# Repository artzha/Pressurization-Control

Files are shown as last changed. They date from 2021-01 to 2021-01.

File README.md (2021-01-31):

# Pressurization-Control
Designed by Josh Azrin and Arthur Zhang.

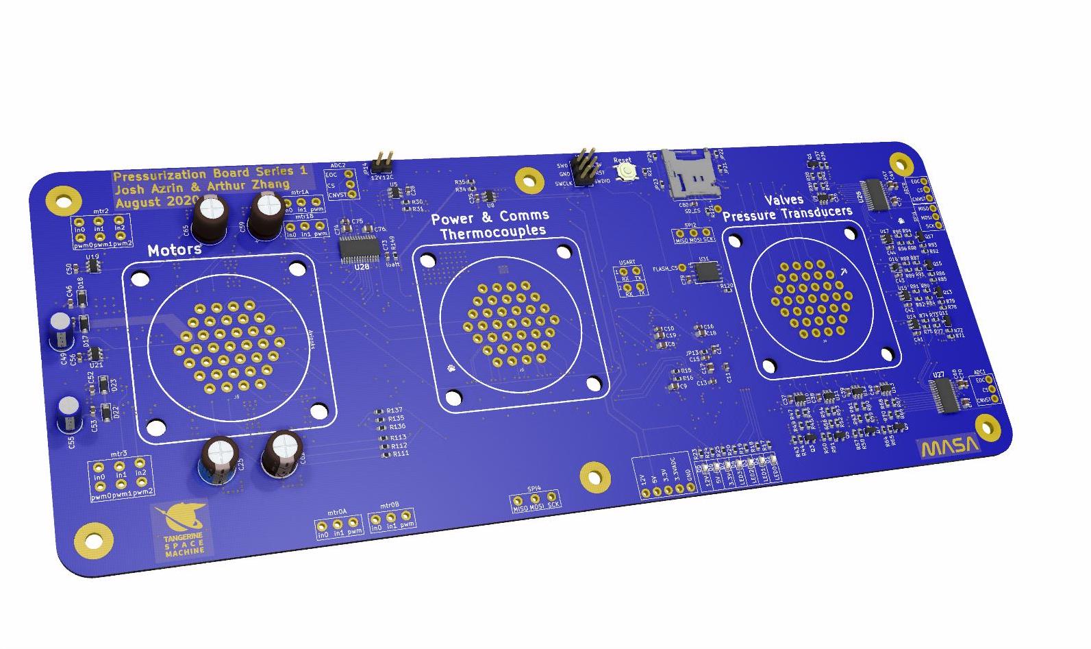
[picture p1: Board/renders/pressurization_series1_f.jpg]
Board Front

|:--:| 
| *Front of PCB* |

Combustion-Control is a project that Josh and I researched and designed to actively balance the liquid fuel tanks for rockets using a PID control loop and various peripherals. We are currently working with the ATLO team to integrate their custom PID control loop into this system. Currently, we are using this PCB on Tangerine Space Machine, a rocket that students are designing at Michigan Aeronautics and Science Association (MASA), a project design team at the University of Michigan.

## Project Overview
1. Overview
1. Board Specs
2. Key Features
3. Firmware Architecture
4. Additional Information

## Overview

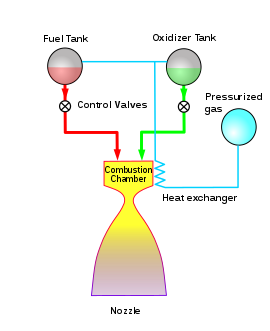
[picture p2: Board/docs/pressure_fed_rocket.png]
Pressure Explanation

|:--:| 
| *Diagram of Pressure Fed Rocket* |

Liquid fuel rockets typically use a pressurized gas like helium to force fuel and oxidizer together into a combustion chamber. In order to maintain a steady combustion, we must ensure that the tank pressures exceed the combustion chamber pressure. We plan on accomplishing this by controlling the flow rate of the the fuel and oxidizer together using a needle valve. This method uses simple plumbing and removes the need for complex turbopumps. Along with Josh, we designed a PCB that supports this functionality. In addition, I have also architected the firmware for carrying out PID control, Command and Data Handling, and interfacing with peripherals.

## Board Specs

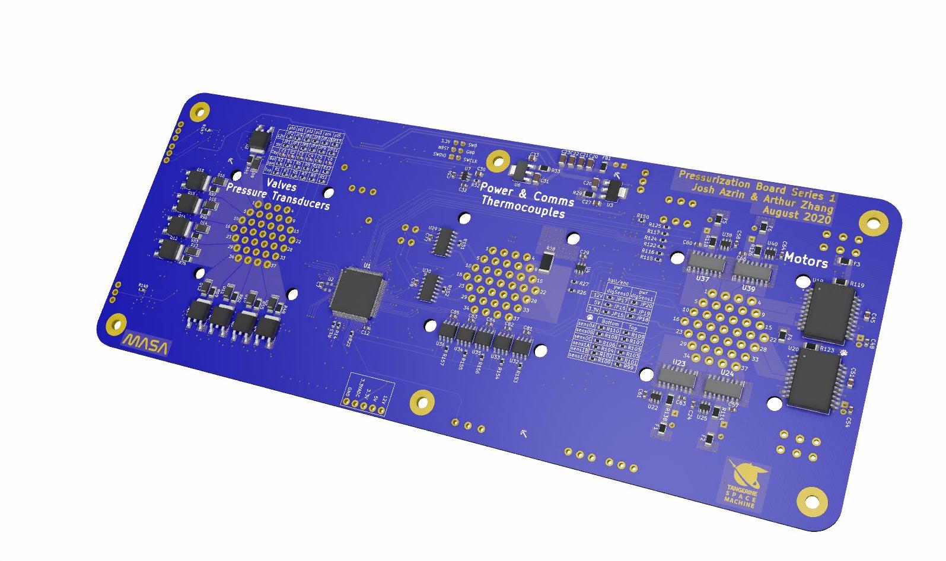
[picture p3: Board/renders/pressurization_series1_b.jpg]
Board Back

|:--:| 
| *Back of PCB* |

The completed board is an eight layer PCB with the stackup
listed below:

* Analog
* Ground
* North South Signals
* 3v3
* 12v
* East West Signals
* Ground Power

We chose to use 8 layers for this iteration for this iteration to reduce the layout
complexity and remove concerns about electromagnetic interference. However, on the
future flight board, I will focus on reducing the number of layers and condensing
the placement of the components.

* 9 Dual State Valves (12V 5A continuous)
* 3 Analog to Digital Converters (12 bit resolution)
* 6 Pressure Transducers
* 4 H-Bridge Motor Drivers (12V 15A)
* 2 Three Phase Motor Drivers
* 6 Hall Effect Sensors
* 2 Potentiometers
* 2 Full Duplex RS-422 Communication Channels
* 5 Thermocouples
* 1 Non-volatile Flash Memory Chip
* 1 Micro SD Card Reader

The board organizational hierachy can be seen in the schematic below.

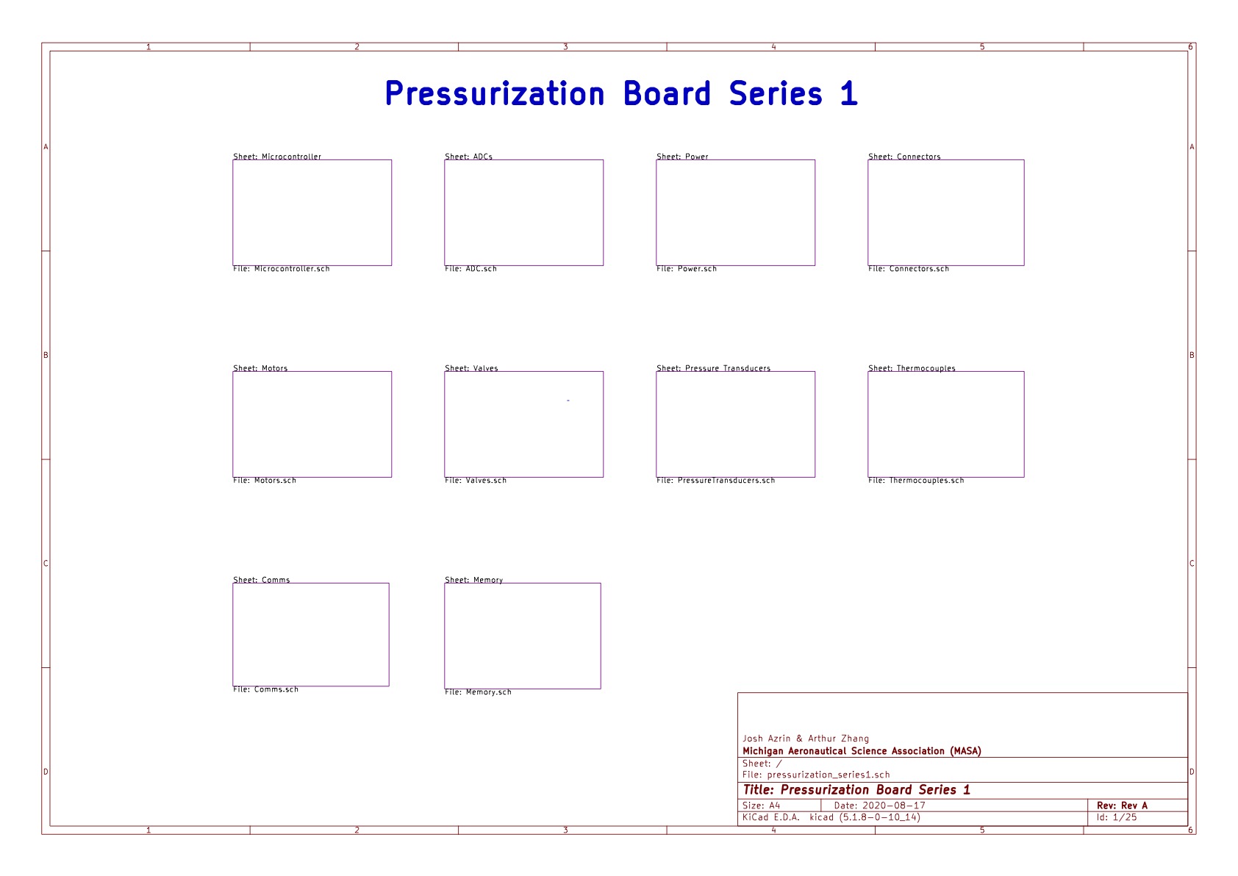
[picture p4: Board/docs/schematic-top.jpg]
Schematic


## Key Features

Utilizing the redundant RS-422 communication chips, the system is able transceive
data with a ground computer with the assistance of a wireless transceiver. This 
becomes extremely important because it gives us the ability to monitor the rocket state for
anomalies and abort the procedure if needed.

In addition, the board supports multiple methods of storing data. During pressurization
tests, we are able to write telemetry directly into non-volatile flash memory and
a micro sd card. This creates an additional level of data redundancy on the board 
in case parts of the system become damaged and unusable during testing. 

## Firmware Architecture

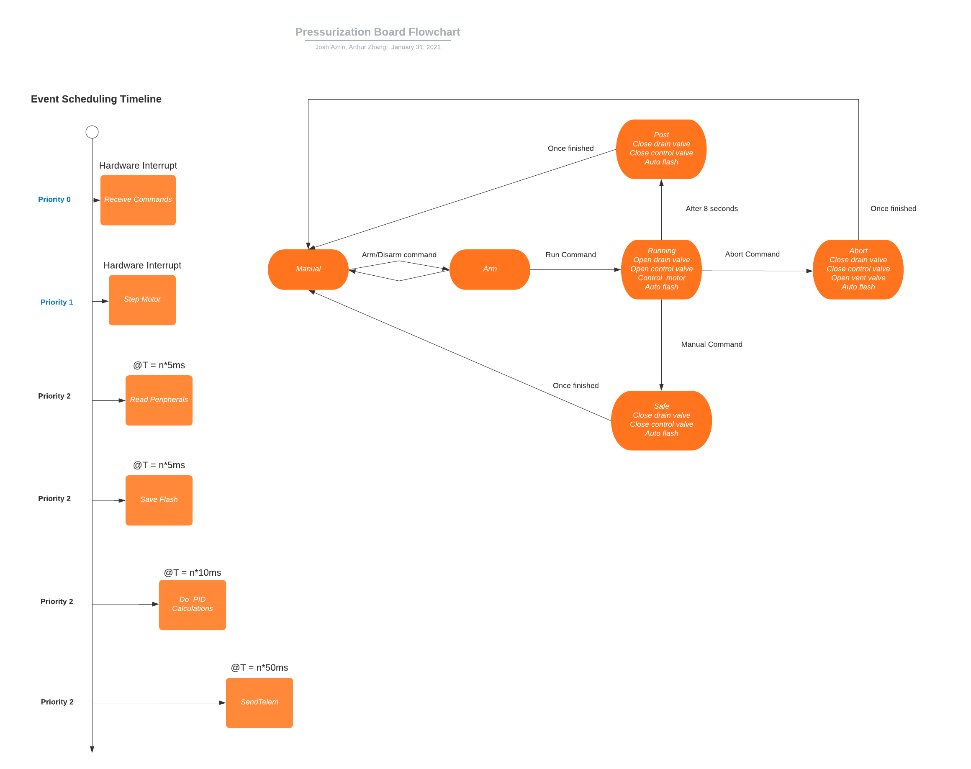
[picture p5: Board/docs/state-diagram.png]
State Diagram

|:--:| 
| *State Diagram of Firmware* |

The system can be one of these various states (in orange) and transitions between 
the Idle, Armed, and Done states by receiving commands from a remote computer. 
These states are for the user to check the system for nominal behavior. In the Running 
and Abort Case Handling states, the board is in control of the system and will continue 
executing the PID control loop until commanded to stop or potentially dangerous 
system behavior is detected. Once the pressurization procedure is proceeded, all of the 
telemetry data logged at high speed is dumped from flash memory to the remote computer
via an ethernet using RS-422.

Because there are several time sensitive tasks that must be completed, I used hardware
timers to guarantee that they are executed precisely. For less critical functions,
the system uses a virtual timer to approximately execute them at the correct time.

Along with writing C code for interfacing with peripherals using SPI and UART, I also
developed a telemetry packet format and firmware for communicating with external 
PCBs and computers. The communication packet COBs encodes data to increase its 
resilence to errors and contains useful information like a 32 bit timestamp, packet
target address, and simple checksum.

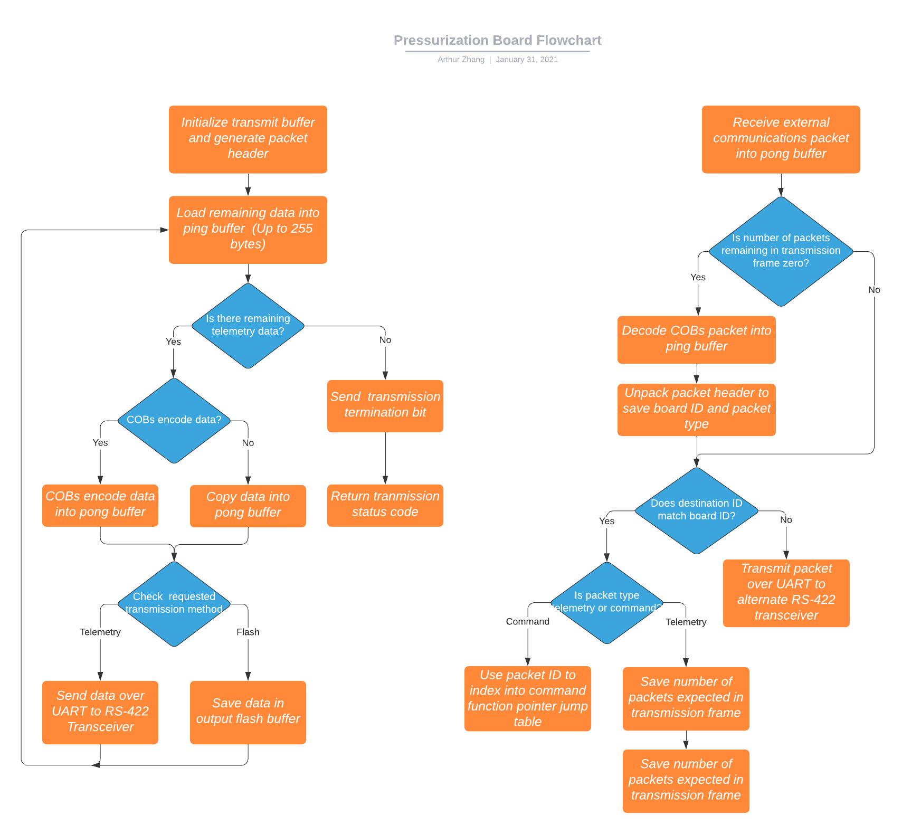
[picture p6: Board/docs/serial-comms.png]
Serial Comms

|:--:| 
| *Logic Flow of Serial Communications Library* |

The serial communication library supports both sending and receiving data over RS-422 transceiver chips, and is capable of handling communications across any amount of daisy chained PCBs. It will become increasingly more important to support daisy chained communications across boards as the rocket becomes more complex because communicatingbetween board to board is highly useful. During both data transmission and reception, the library utilizes a two buffer system for loading and encoding data. By doing this, the system can be easily adapted to a design where an external chip can write telemetry data directly to memory on the microcontroller before it is encoded by the library. This allows for parallel processing of data preparation and transmission. 

The library also provides users with the ability to COBs encode data prior to transmission. Using COBs encoding, 
otherwise known as Consistent Overhead Byte Stuffing, saves a significant amount of memory on the microcontroller 
because the algorithm allows boards to unambiguously terminate each transmission frame with a unique termination bit. It does this by replacing all occurrences of a terminator bit in the message with a byte representing the number of spaces until the next terminator bit. The algorithm also guarantees that it will add exactly two bytes to each transmission frame, which allows us to calculate the number of packets that will be sent  in the next transmission frame and include this information in the packet header. 

For additional information on the firmware architecture, please consult me (Arthur Zhang)
and I will be happy to discuss more details on its implementation.

## Additional Information

### Project Setup Details

This project uses KiCAD, a free PCB and schematic design tool. It uses the default
schematic, footprint, and 3d model library paths. In addition, the repository for
firmware is built on the STM32CubeIDE platform.

### Reviewers

Special thanks to Marion Anderson and Alex Davenport for constantly reviewing and 
providing guidance on this project.

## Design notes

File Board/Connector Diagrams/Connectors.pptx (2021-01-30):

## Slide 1

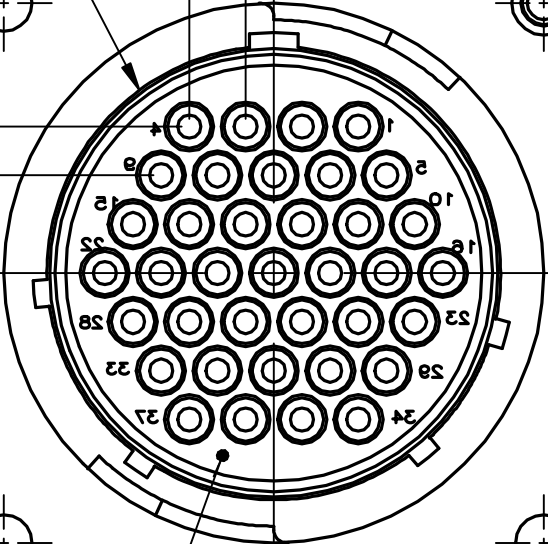
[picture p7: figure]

+

+

+

Power, Comms & Thermocouples
Connector Diagram Legend:
P: Power
G: Ground
R+: RS422 receive (positive differential)
R-: RS422 receive (negative differential)
T+: RS422 transmit (positive differential)
T-: RS422 transmit (negative differential)
+: One side of tc
-: Other side tc
Red: Battery
Blue: Comms
Green: Thermocouples
Board Connector: 2-208224-1 or similar
Harness Connector: 206305-1 or similar
Board pinout MATCHES connector pinout
Diagram is for both
connector and board pinout

G

G

G

G

Batt-

P

P

P

G

P

Batt+

G

Rs-2

R+

R-

T-

T+

P

P

GP
IO-0

GP
IO-1

GP
IO-2

R+

Rs-1

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
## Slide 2

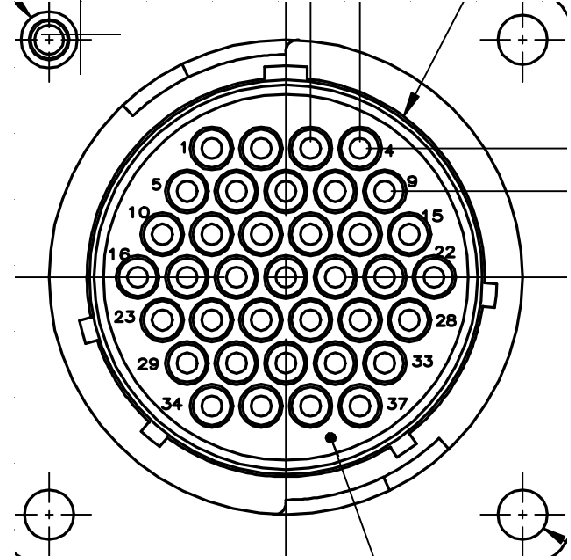
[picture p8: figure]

Motor Connector Diagram Legend:
P: Power
G: Ground
S: Signal
A, B, C: phases for motor
A, B, C: Digital sensor (encoder or hall)
output signals
+: One side of motor/valve
-: Other side of motor/valve
Red: Motors
Blue: Potentiometers
Yellow: Digital sensor
Board Connector: 1-206934-4 or similar
Harness Connector: 206150-1 or similar
Board pinout MIRRORS connector pinout
about the vertical axis numerically
Diagram is for connector pinout only!
Board pinout is mirrored

B

+

mtr1A

pot1

G

G

mtr2

pot3

S

G

A

P

pot2

G

P

mtr1B

S

S

+

C

B

P

dig0

P

pot0

G

P

S

mtr3

A

A

dig0

C

+

mtr0B

B

P

dig1

G

C

A

dig1

C

B

+

mtr0A

enc0

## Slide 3

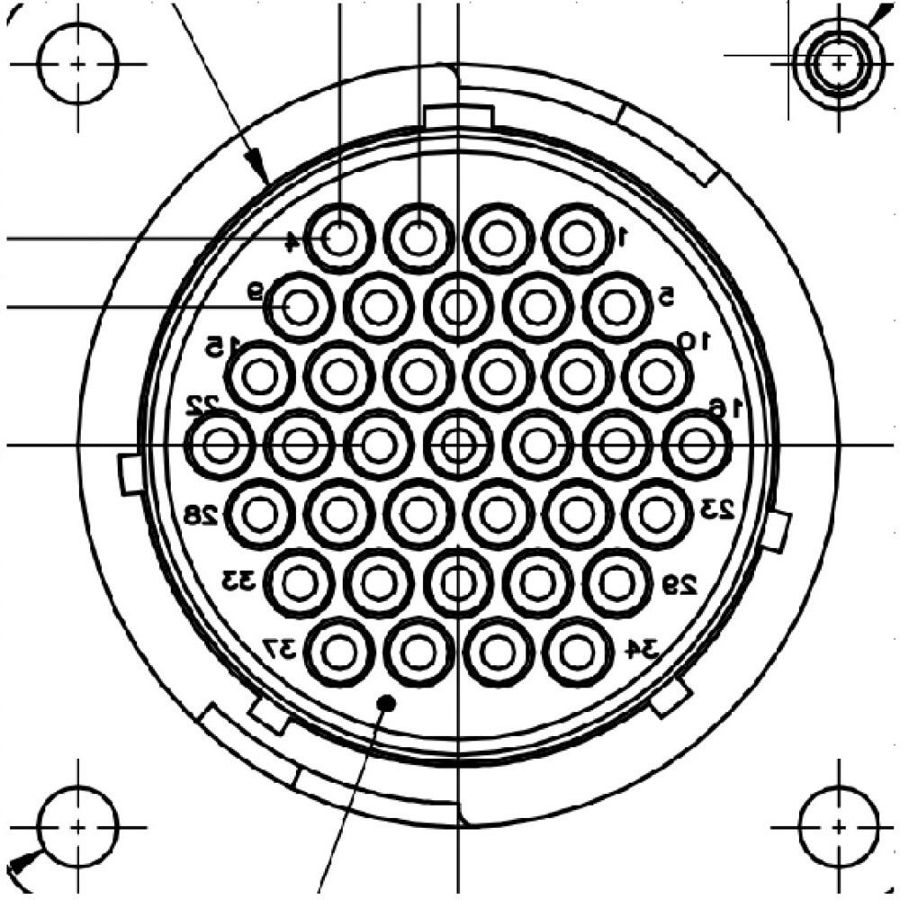
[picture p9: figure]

Valve & Pressure Transducer
Connector Diagram Legend:
P: Power
G: Ground
S: Signal
+: One side of motor/valve
-: Other side of motor/valve
Red: Valves
Blue: Pressure Transducers
Board Connector: 2-208224-1 or similar
Harness Connector: 206305-1 or similar
Board pinout MATCHES connector pinout
Diagram is for both
connector and board pinout

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
vlv0

+

P

G

P

G

vlv8

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
vlv7

G

P

G

G

vlv5

vlv6

+

vlv1

vlv2

vlv3

vlv4

+

+

+

+

+

P

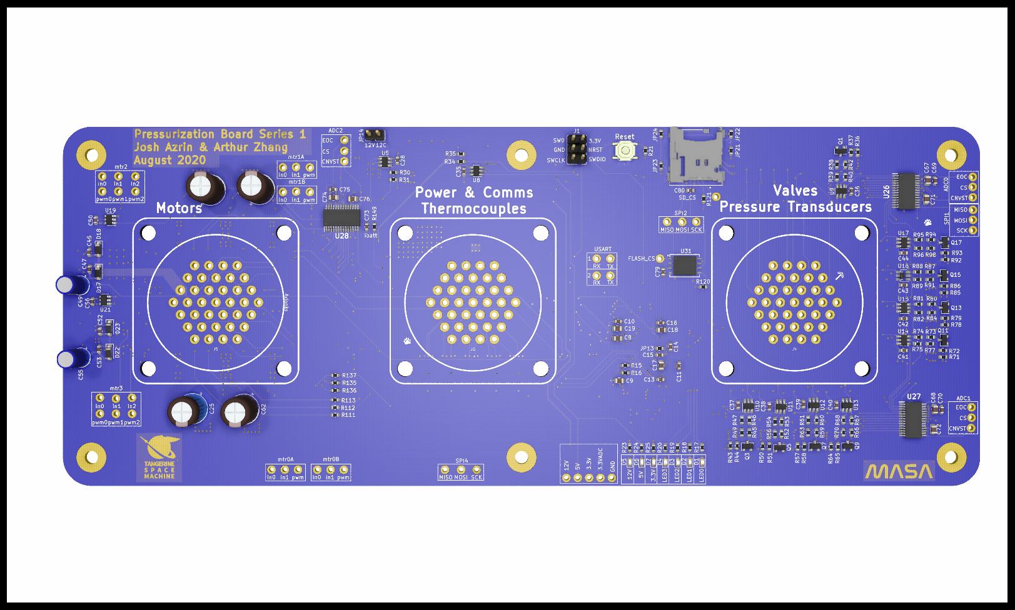
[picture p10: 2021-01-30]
Board/renders/pressurization_series1_front.jpg

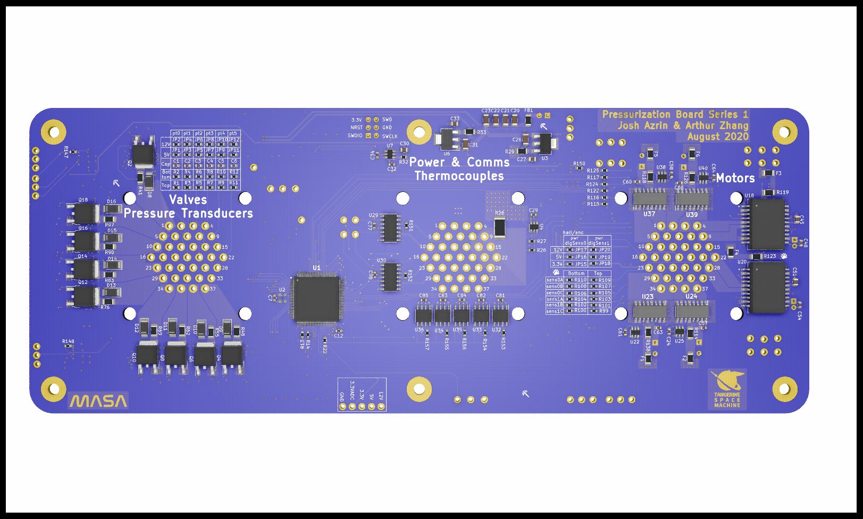
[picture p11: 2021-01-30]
Board/renders/pressurization_series1_back.jpg

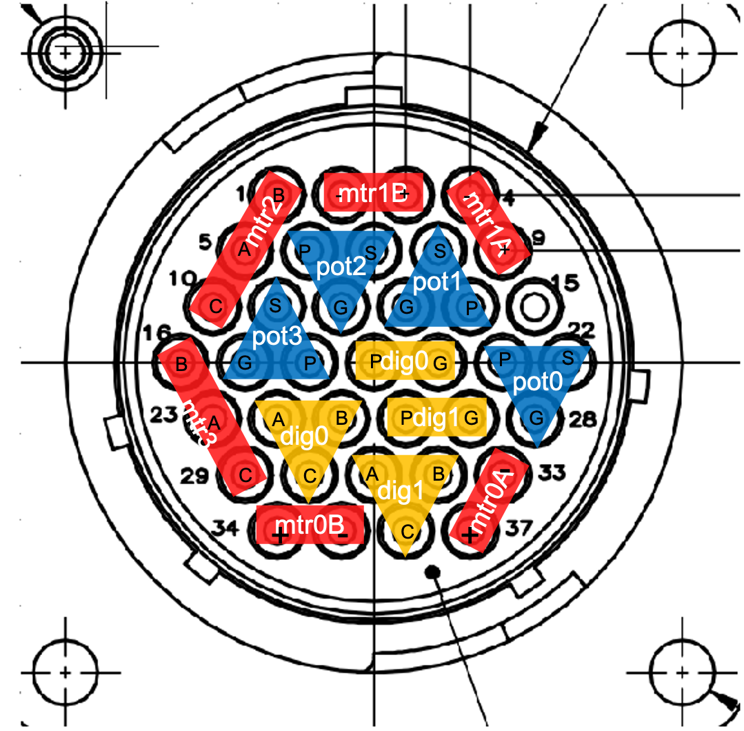
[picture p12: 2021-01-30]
Board/Connector Diagrams/Motors.png

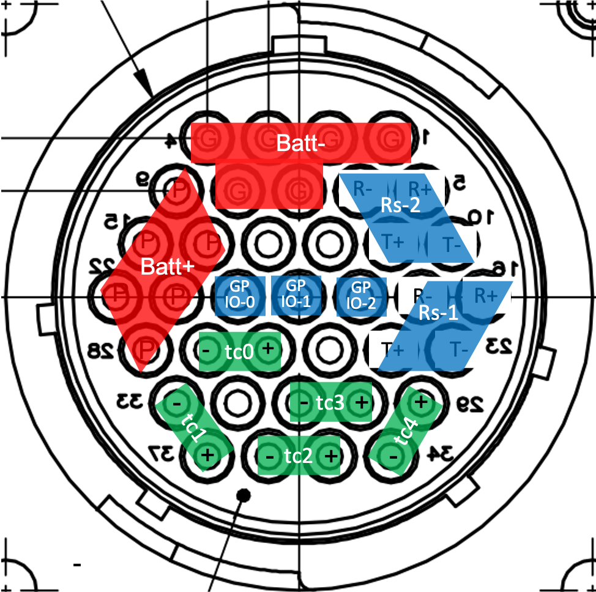
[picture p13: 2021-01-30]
Board/Connector Diagrams/Power&Comms&Tcs.png

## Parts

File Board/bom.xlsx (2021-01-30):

Id | Designator | Package | Quantity | Designation | Inventory | Needed
1 | J5,J6,J4 | 2-208224-2 | 3 | Conn_01x37_Female
5 | G***,G***,G***,G*** | bearpaw_noclaws | 4 | LOGO
12 | C56,C66,C64,C60,C58,C57,C24,C34,C85,C84,C83,C82,C81,C80,C79,C78,C77,C75,C70,C69,C63,C61,C50,C44,C43,C42,C41,C40,C39,C38,C37,C36,C35,C29,C28,C16,C15,C14,C13,C12,C11,C10,C7 | C_0603_1608Metric | 43 | 100n
24 | C32 | C_0603_1608Metric | 1 | 300pf
27 | C53,C47 | C_0603_1608Metric | 2 | 0.22u
30 | C54,C48 | C_0603_1608Metric | 2 | 0.1u
32 | C46,C52 | C_0603_1608Metric | 2 | 10n
37 | C73,C1,C2,C3,C4,C5,C6 | C_0603_1608Metric | 7 | C
25 | C30,C45,C51 | C_0805_2012Metric | 3 | 1u
28 | C76,C72,C71 | C_0805_2012Metric | 3 | u47
29 | C74,C68,C67,C33,C27,C19,C18,C17 | C_0805_2012Metric | 8 | 10u
38 | C8,C9 | C_0805_2012Metric | 2 | 2u2
31 | C31,C20,C21,C22,C23,C26 | C_1206_3216Metric | 6 | 10u
33 | C49,C55 | CP_Radial_D5.0mm_P2.00mm | 2 | 100u
3 | C65,C59,C25,C62 | CP_Radial_D8.0mm_P3.50mm | 4 | 270u
41 | D17,D18,D22,D23 | D_SOD-123 | 4 | 1n4148
40 | D8,D9,D10,D11,D13,D14,D15,D16,D12 | D_SOD-128 | 9 | D
13 | F4,F6,F5,F2,F3,F1 | Fuse_1206_3216Metric | 6 | Fuse
9 | U20,U18 | L6234PD | 2 | L6234PD
39 | D1,D2,D3,D4,D5,D6,D7 | LED_0603_1608Metric | 7 | LED
7 | G***,G*** | MASA_LOGO | 2 | LOGO
36 | U28,U26,U27 | MAX11131AUI+ | 3 | MAX11131AUI+
2 | J3 | MOLEX_503182-1852 | 1 | 503182-1852
26 | MH1,MH6,MH5,MH2,MH3,MH4 | MountingHole-EC3 | 6 | MountingHole
53 | U2 | Oscillator_SMD_EuroQuartz_XO32-4Pin_3.2x2.5mm | 1 | DSC6001CI2A-016.0000T
4 | G***,G***,G***,G*** | pickaxe | 4 | LOGO
45 | JP14 | PinHeader_1x02_P2.54mm_Vertical | 1 | Jumper
43 | J1 | PinHeader_2x03_P2.54mm_Vertical | 1 | Conn_02x03_Counter_Clockwise
14 | R99,R149,R1,R2,R3,R4,R5,R6,R7,R8,R9,R10,R11,R12,R100,R101,R102,R103,R104,R105,R106,R107,R108,R109,R110 | R_0603_1608Metric | 25 | R
15 | R136,R125,R124,R122,R117,R116,R115,R113,R112,R111,R32,R21,R24,R25,R30,R31,R34,R35,R36,R37,R38,R43,R44,R45,R50,R51,R52,R57,R58,R59,R71,R72,R73,R78,R79,R80,R85,R86,R87,R92,R93,R94,R64,R65,R66,R135,R137 | R_0603_1608Metric | 47 | 1k
19 | R121,R120,R150,R13,R14,R15,R16,R22,R147,R148,R155,R153,R157,R154,R156 | R_0603_1608Metric | 15 | Rt
44 | JP1,JP2,JP3,JP4,JP5,JP6,JP7,JP8,JP9,JP10,JP11,JP12,JP13,JP15,JP16,JP17,JP18,JP19,JP20,JP21,JP22,JP23,JP24 | R_0603_1608Metric | 23 | Jumper
47 | R17,R18,R19,R20 | R_0603_1608Metric | 4 | 220
48 | R23,R26,R39,R42,R46,R49,R53,R56,R60,R63,R74,R77,R81,R84,R88,R91,R95,R98,R67,R70 | R_0603_1608Metric | 20 | 10k
49 | R27,R40,R47,R54,R61,R75,R82,R89,R96,R68 | R_0603_1608Metric | 10 | 3k3
50 | R151,R152 | R_0603_1608Metric | 2 | 100
11 | R123,R126,R118,R114,R41,R48,R55,R62,R76,R83,R90,R97,R69,R119,R138 | R_1206_3216Metric | 15 | 5m
34 | R29,R33 | R_1206_3216Metric | 2 | 40m
42 | FB1 | R_1206_3216Metric | 1 | Ferrite_Bead
35 | R28 | R_2512_6332Metric | 1 | 1m
8 | J2 | short | 1 | GS2
22 | U30,U29 | SOIC-14_3.9x8.7mm_P1.27mm | 2 | MAX3491
56 | U34,U32,U36,U33,U35 | SOIC-8_3.9x4.9mm_P1.27mm | 5 | MAX31855KASA
55 | U31 | SON127P800X600X80-9N | 1 | W25N01GVZEIG
21 | U3 | SOT-223 | 1 | TL1963A-33DCYR
54 | U6 | SOT-223 | 1 | LM2931
46 | Q1,Q3,Q5,Q7,Q11,Q13,Q15,Q17,Q9 | SOT-23 | 9 | MMBT3904
10 | U19,U21 | SOT-23-6 | 2 | INA181AX
52 | U1 | STM32F446VET6 | 1 | STM32F446VET6
51 | SW1 | SW4-SMD-5.2X5.2X1.5MM | 1 | SMD-BUTTON
18 | TP54,TP53,TP52,TP51,TP50,TP47,TP32,TP31,TP30,TP49,TP48,TP46,TP35,TP38,TP41,TP1,TP2,TP3,TP4,TP5,TP6,TP7,TP8,TP9,TP10,TP11,TP12,TP13,TP15,TP16,TP17,TP18,TP19,TP20,TP21,TP22,TP23,TP24,TP25,TP26,TP27,TP28,TP29,TP33,TP34,TP36,TP37,TP39,TP40,TP42,TP43,TP44,TP45 | TestPoint-EC3 | 53 | TestPoint
20 | Q16,Q6,Q8,Q4,Q2,Q12,Q14,Q18,Q10 | TO-252-2 | 9 | Q_PMOS_GDS
6 | G***,G*** | TSM_Logo | 2 | LOGO
16 | U25,U40,U38,U4,U13,U5,U8,U9,U10,U11,U12,U14,U15,U16,U17,U22 | TSOT-23-6 | 16 | INA181AX
23 | U7 | TSOT-23-6 | 1 | MCP1501
17 | U39,U37,U24,U23 | VNH7070ASTR | 4 | VNH7070ASTR

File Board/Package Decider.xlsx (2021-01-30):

Resistor
Resistance (ohms) | Max current (A) | Power (W) | Use | Package | Link
0.001 | 78 | 6.084 | Battery | 2512 | https://www.digikey.com/product-detail/en/bourns-inc/CSS2H-2512R-1L00F/CSS2H-2512R-1L00FCT-ND/6023725 | Note: 5W resistor b/c that's what the EC used. 78A from 13A per connector pin times 6 connector pins
0.005 | 15 | 1.125 | Motor and Valves | 1206 | https://www.digikey.com/product-detail/en/koa-speer-electronics-inc/TLR2BPDTD5L00F75/2019-TLR2BPDTD5L00F75CT-ND/9847556
0.04 | 1.5 | 0.09 | 3.3V,5V |  | https://www.digikey.com/products/en/resistors/chip-resistor-surface-mount/52?k=resistors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
Eletrolytic Capacitors
Capacitance | Voltage Rating | Package | Link
100uF | >12V | D6.3 mm L7.7 mm | https://industrial.panasonic.com/cdbs/www-data/pdf/RDE0000/DME0000COL90.pdf
270uF | >12V | D6.3 mm L7.7 mm | https://www.digikey.com/product-detail/en/panasonic-electronic-components/EEE-FKC271XSP/P18951CT-ND/5805058
Ceramic Capacitors
Capacitance | Voltage Rating | Package | Link
1uF | >12V | 805 | https://www.digikey.com/product-detail/en/kemet/C1206C105M4RACTU/399-8150-2-ND/2215103
2.2uF | >12V | 805 | https://www.digikey.com/product-detail/en/kemet/C1206C225K5RECAUTO/399-17896-2-ND/8640490
10uF | >12V | 805 | https://www.digikey.com/product-detail/en/kemet/C1206C106M3PACTU/399-8153-2-ND/2215120

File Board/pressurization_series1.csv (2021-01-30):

Id | Designator | Package | Quantity | Designation | Supplier and ref
1 | J5,J6,J4 | 2-208224-2 | 3 | Conn_01x37_Female
2 | J3 | MOLEX_503182-1852 | 1 | 503182-1852
3 | C65,C59,C25,C62 | CP_Radial_D8.0mm_P3.50mm | 4 | 270u
4 | G***,G***,G***,G*** | pickaxe | 4 | LOGO
5 | G***,G***,G***,G*** | bearpaw_noclaws | 4 | LOGO
6 | G***,G*** | TSM_Logo | 2 | LOGO
7 | G***,G*** | MASA_LOGO | 2 | LOGO
8 | J2 | short | 1 | GS2
9 | U20,U18 | L6234PD | 2 | L6234PD
10 | U19,U21 | SOT-23-6 | 2 | INA181AX
11 | R123,R126,R118,R114,R41,R48,R55,R62,R76,R83,R90,R97,R69,R119,R138 | R_1206_3216Metric | 15 | 5m
12 | C56,C66,C64,C60,C58,C57,C24,C34,C85,C84,C83,C82,C81,C80,C79,C78,C77,C75,C70,C69,C63,C61,C50,C44,C43,C42,C41,C40,C39,C38,C37,C36,C35,C29,C28,C16,C15,C14,C13,C12,C11,C10,C7 | C_0603_1608Metric | 43 | 100n
13 | F4,F6,F5,F2,F3,F1 | Fuse_1206_3216Metric | 6 | Fuse
14 | R99,R149,R1,R2,R3,R4,R5,R6,R7,R8,R9,R10,R11,R12,R100,R101,R102,R103,R104,R105,R106,R107,R108,R109,R110 | R_0603_1608Metric | 25 | R
15 | R136,R125,R124,R122,R117,R116,R115,R113,R112,R111,R32,R21,R24,R25,R30,R31,R34,R35,R36,R37,R38,R43,R44,R45,R50,R51,R52,R57,R58,R59,R71,R72,R73,R78,R79,R80,R85,R86,R87,R92,R93,R94,R64,R65,R66,R135,R137 | R_0603_1608Metric | 47 | 1k
16 | U25,U40,U38,U4,U13,U5,U8,U9,U10,U11,U12,U14,U15,U16,U17,U22 | TSOT-23-6 | 16 | INA181AX
17 | U39,U37,U24,U23 | VNH7070ASTR | 4 | VNH7070ASTR
18 | TP54,TP53,TP52,TP51,TP50,TP47,TP32,TP31,TP30,TP49,TP48,TP46,TP35,TP38,TP41,TP1,TP2,TP3,TP4,TP5,TP6,TP7,TP8,TP9,TP10,TP11,TP12,TP13,TP15,TP16,TP17,TP18,TP19,TP20,TP21,TP22,TP23,TP24,TP25,TP26,TP27,TP28,TP29,TP33,TP34,TP36,TP37,TP39,TP40,TP42,TP43,TP44,TP45 | TestPoint-EC3 | 53 | TestPoint
19 | R121,R120,R150,R13,R14,R15,R16,R22,R147,R148,R155,R153,R157,R154,R156 | R_0603_1608Metric | 15 | Rt
20 | Q16,Q6,Q8,Q4,Q2,Q12,Q14,Q18,Q10 | TO-252-2 | 9 | Q_PMOS_GDS
21 | U3 | SOT-223 | 1 | TL1963A-33DCYR
22 | U30,U29 | SOIC-14_3.9x8.7mm_P1.27mm | 2 | MAX3491
23 | U7 | TSOT-23-6 | 1 | MCP1501
24 | C32 | C_0603_1608Metric | 1 | 300pf
25 | C30,C45,C51 | C_0805_2012Metric | 3 | 1u
26 | MH1,MH6,MH5,MH2,MH3,MH4 | MountingHole-EC3 | 6 | MountingHole
27 | C53,C47 | C_0603_1608Metric | 2 | 0.22u
28 | C76,C72,C71 | C_0805_2012Metric | 3 | u47
29 | C74,C68,C67,C33,C27,C19,C18,C17 | C_0805_2012Metric | 8 | 10u
30 | C54,C48 | C_0603_1608Metric | 2 | 0.1u
31 | C31,C20,C21,C22,C23,C26 | C_1206_3216Metric | 6 | 10u
32 | C46,C52 | C_0603_1608Metric | 2 | 10n
33 | C49,C55 | CP_Radial_D5.0mm_P2.00mm | 2 | 100u
34 | R29,R33 | R_1206_3216Metric | 2 | 40m
35 | R28 | R_2512_6332Metric | 1 | 1m
36 | U28,U26,U27 | MAX11131AUI+ | 3 | MAX11131AUI+
37 | C73,C1,C2,C3,C4,C5,C6 | C_0603_1608Metric | 7 | C
38 | C8,C9 | C_0805_2012Metric | 2 | 2u2
39 | D1,D2,D3,D4,D5,D6,D7 | LED_0603_1608Metric | 7 | LED
40 | D8,D9,D10,D11,D13,D14,D15,D16,D12 | D_SOD-128 | 9 | D
41 | D17,D18,D22,D23 | D_SOD-123 | 4 | 1n4148
42 | FB1 | R_1206_3216Metric | 1 | Ferrite_Bead
43 | J1 | PinHeader_2x03_P2.54mm_Vertical | 1 | Conn_02x03_Counter_Clockwise
44 | JP1,JP2,JP3,JP4,JP5,JP6,JP7,JP8,JP9,JP10,JP11,JP12,JP13,JP15,JP16,JP17,JP18,JP19,JP20,JP21,JP22,JP23,JP24 | R_0603_1608Metric | 23 | Jumper
45 | JP14 | PinHeader_1x02_P2.54mm_Vertical | 1 | Jumper
46 | Q1,Q3,Q5,Q7,Q11,Q13,Q15,Q17,Q9 | SOT-23 | 9 | MMBT3904
47 | R17,R18,R19,R20 | R_0603_1608Metric | 4 | 220
48 | R23,R26,R39,R42,R46,R49,R53,R56,R60,R63,R74,R77,R81,R84,R88,R91,R95,R98,R67,R70 | R_0603_1608Metric | 20 | 10k
49 | R27,R40,R47,R54,R61,R75,R82,R89,R96,R68 | R_0603_1608Metric | 10 | 3k3
50 | R151,R152 | R_0603_1608Metric | 2 | 100
51 | SW1 | SW4-SMD-5.2X5.2X1.5MM | 1 | SMD-BUTTON
52 | U1 | STM32F446VET6 | 1 | STM32F446VET6
53 | U2 | Oscillator_SMD_EuroQuartz_XO32-4Pin_3.2x2.5mm | 1 | DSC6001CI2A-016.0000T
54 | U6 | SOT-223 | 1 | LM2931
55 | U31 | SON127P800X600X80-9N | 1 | W25N01GVZEIG
56 | U34,U32,U36,U33,U35 | SOIC-8_3.9x4.9mm_P1.27mm | 5 | MAX31855KASA

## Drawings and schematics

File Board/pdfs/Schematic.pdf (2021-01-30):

Josh Azrin & Arthur Zhang
File: pressurization_series1.sch Sheet: / Michigan Aeronautical Science Association (MASA)

Id: 1/25 Title: Pressurization Board Series 1

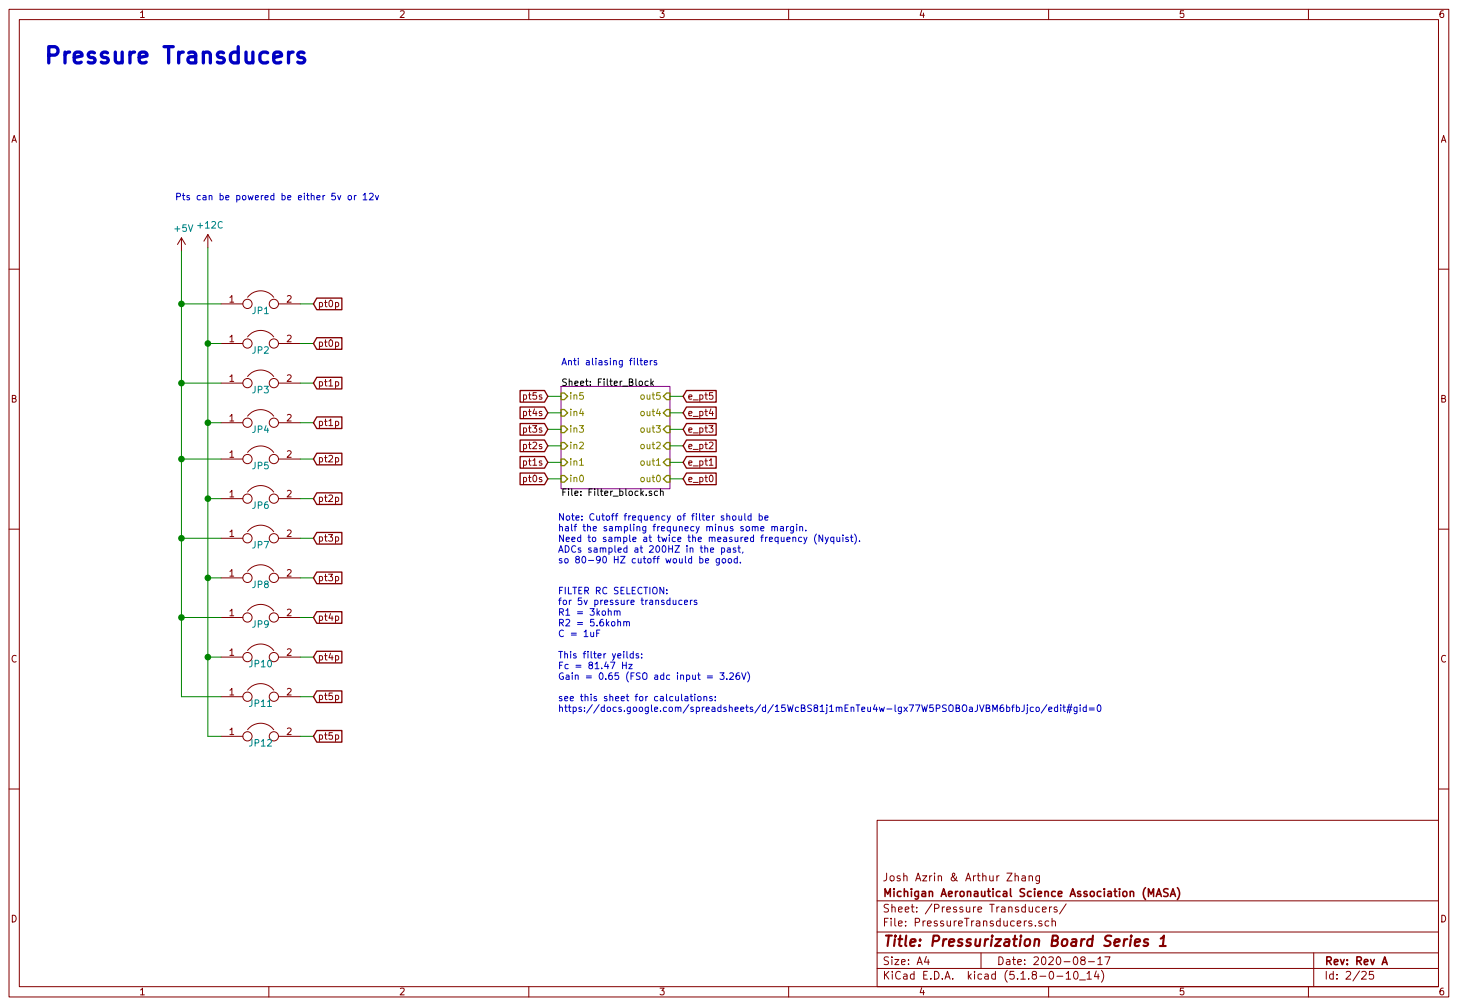
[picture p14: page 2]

Pts can be powered be either 5v or 12v

Note: Cutoff frequency of filter should be
half the sampling frequnecy minus some margin.
Need to sample at twice the measured frequency (Nyquist).
ADCs sampled at 200HZ in the past,
so 80-90 HZ cutoff would be good. FILTER RC SELECTION:

This filter yeilds: Fc = 81.47 Hz Gain = 0.65 (FSO adc input = 3.26V) see this sheet for calculations: https://docs.google.com/spreadsheets/d/15WcBS81j1mEnTeu4w-lgx77W5PSOBOaJVBM6bfbJjco/edit#gid=0

Josh Azrin & Arthur Zhang
File: PressureTransducers.sch Sheet: /Pressure Transducers/ Michigan Aeronautical Science Association (MASA)

Id: 2/25 Title: Pressurization Board Series 1

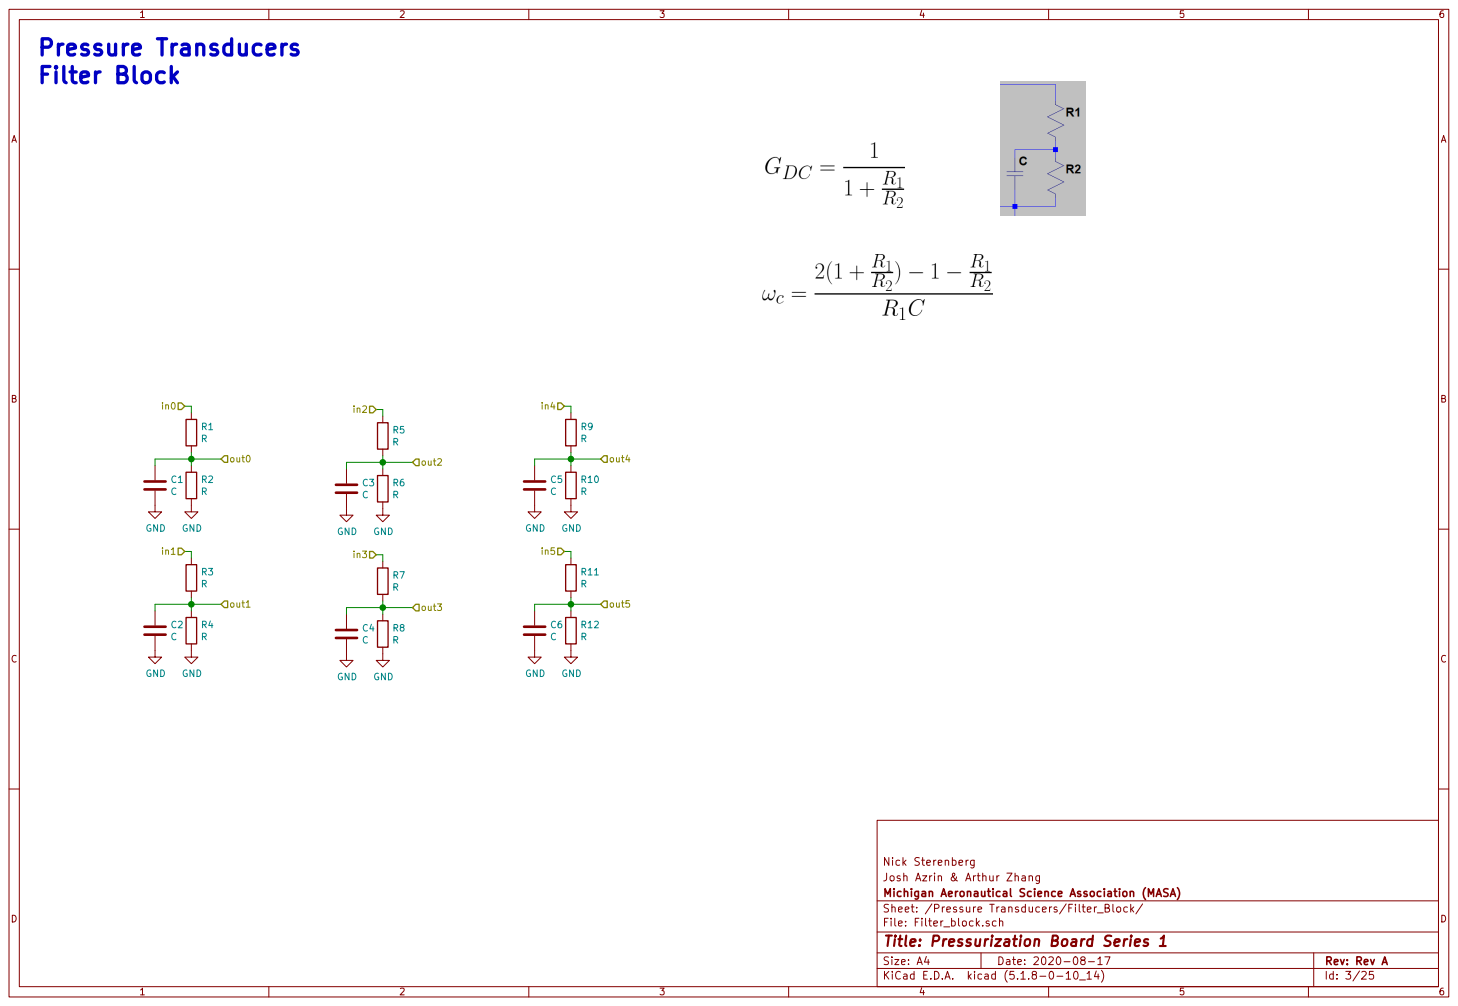
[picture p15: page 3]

Josh Azrin & Arthur Zhang
Michigan Aeronautical Science Association (MASA)
Sheet: /Pressure Transducers/Filter_Block/
File: Filter_block.sch
Id: 3/25 Title: Pressurization Board Series 1

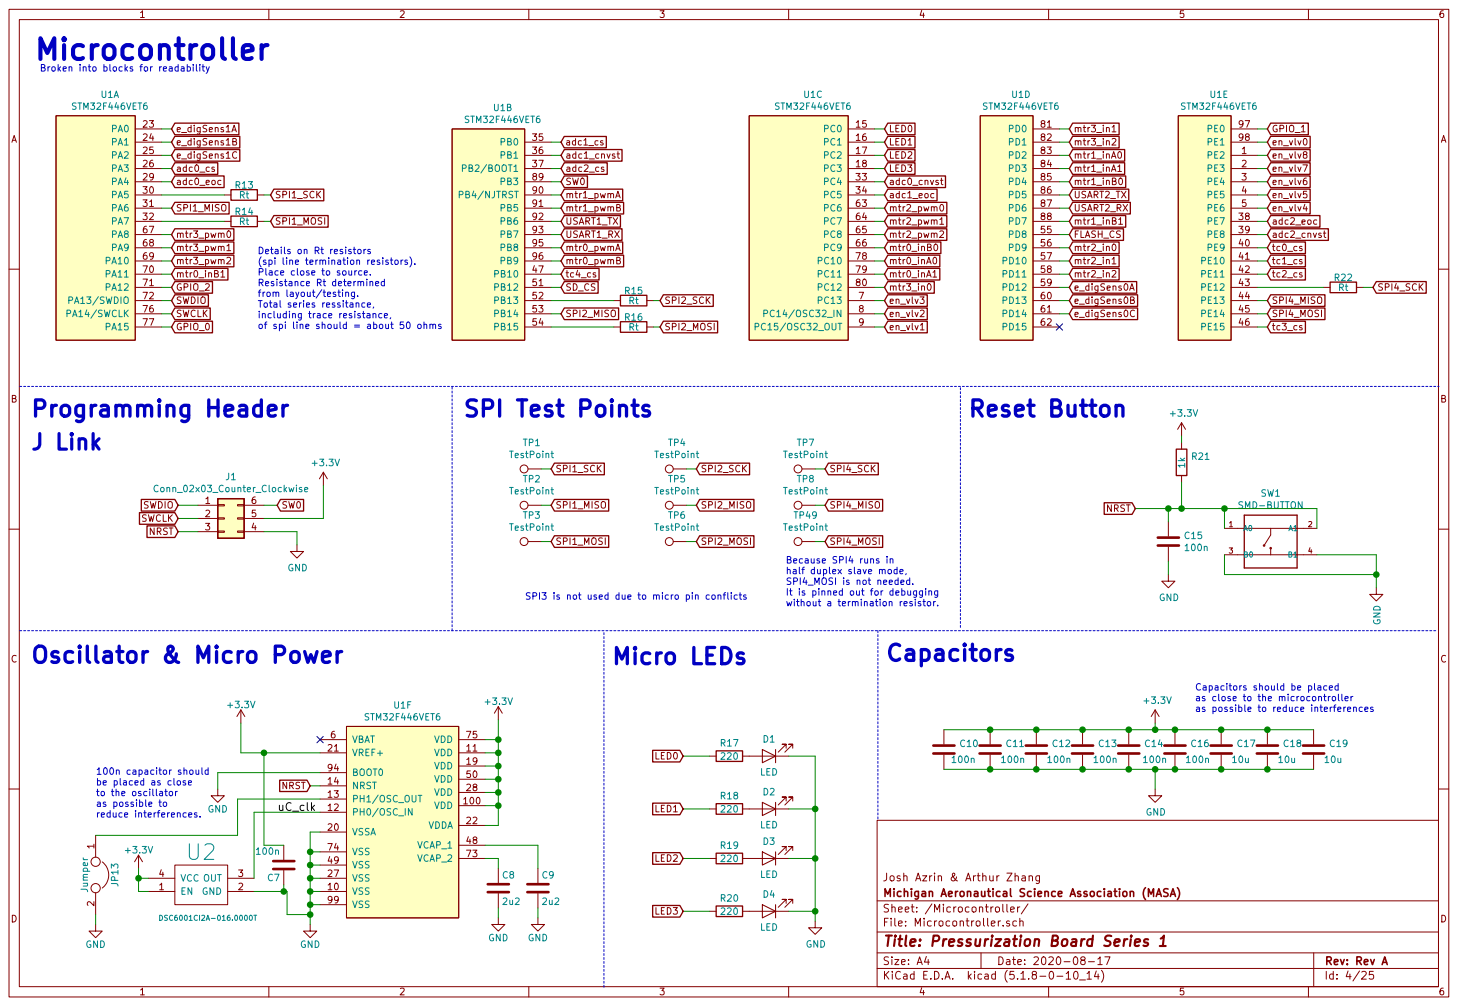
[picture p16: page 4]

en_vlv6 NRST
mtr1_pwmA GPIO_0
SPI1_MISO
to the oscillator as possible to reduce interferences. J Link

from layout/testing. Total series ressitance,

including trace resistance,
of spi line should = about 50 ohms

Because SPI4 runs in half duplex slave mode, SPI4_MOSI is not needed.

It is pinned out for debugging without a termination resistor. SPI3 is not used due to micro pin conflicts

Capacitors should be placed as close to the microcontroller as possible to reduce interferences

100n capacitor should
be placed as close

Josh Azrin & Arthur Zhang
File: Microcontroller.sch Sheet: /Microcontroller/ Michigan Aeronautical Science Association (MASA)

Id: 4/25 Title: Pressurization Board Series 1

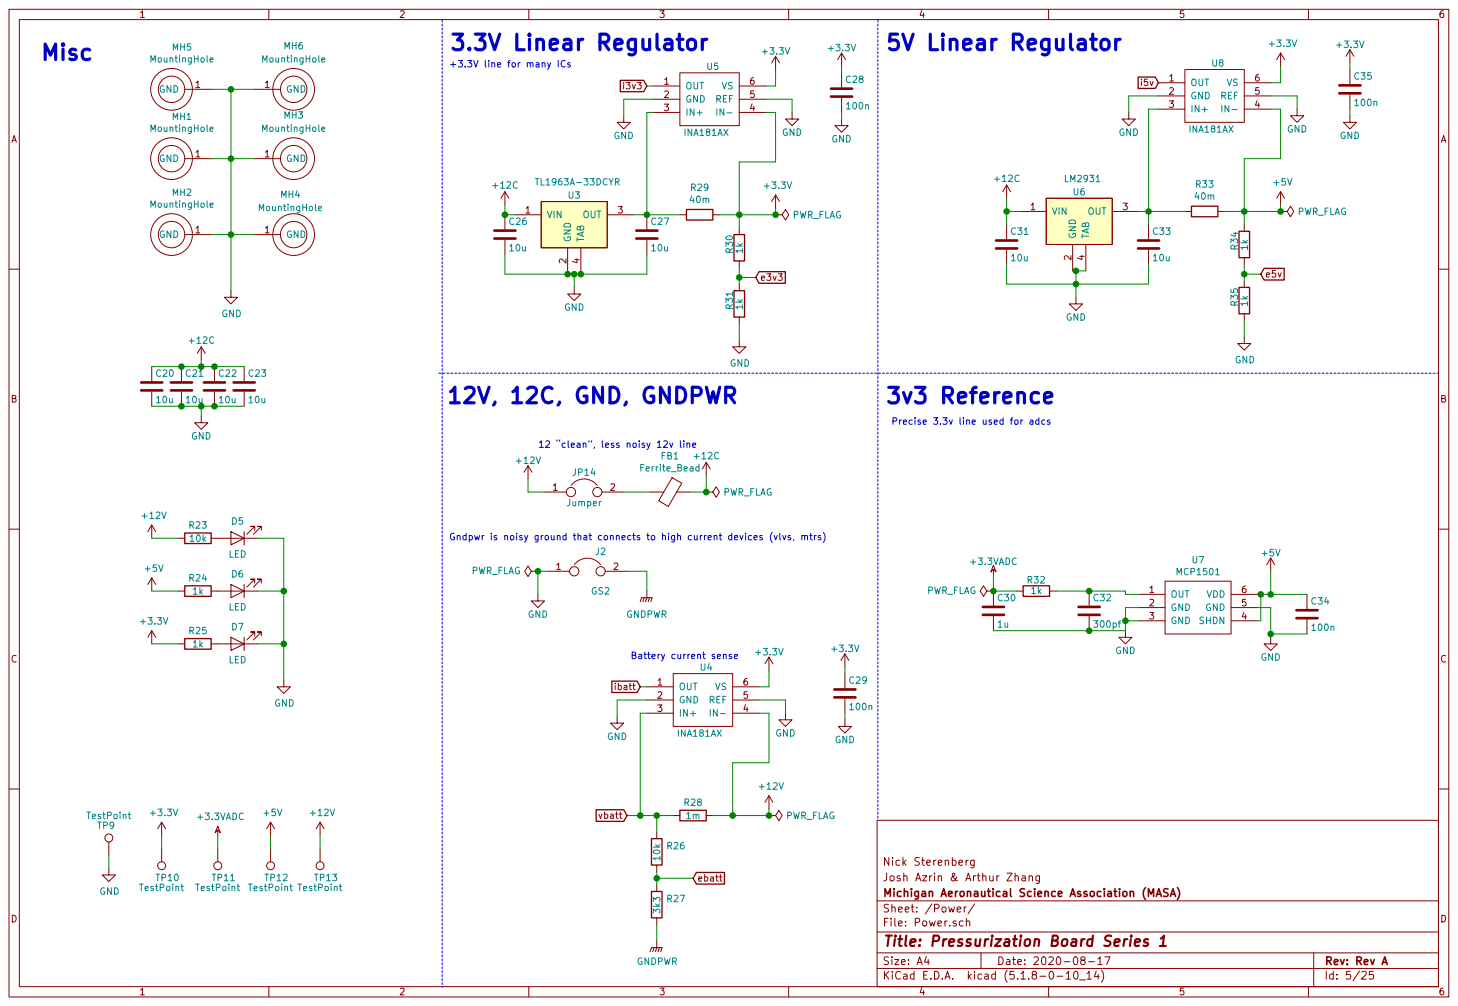
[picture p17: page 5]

+3.3V line for many ICs

Precise 3.3v line used for adcs 12 clean, less noisy 12v line

Gndpwr is noisy ground that connects to high current devices (vlvs, mtrs)

Nick Sterenberg
Josh Azrin & Arthur Zhang
File: Power.sch Sheet: /Power/ Michigan Aeronautical Science Association (MASA)

Id: 5/25 Title: Pressurization Board Series 1

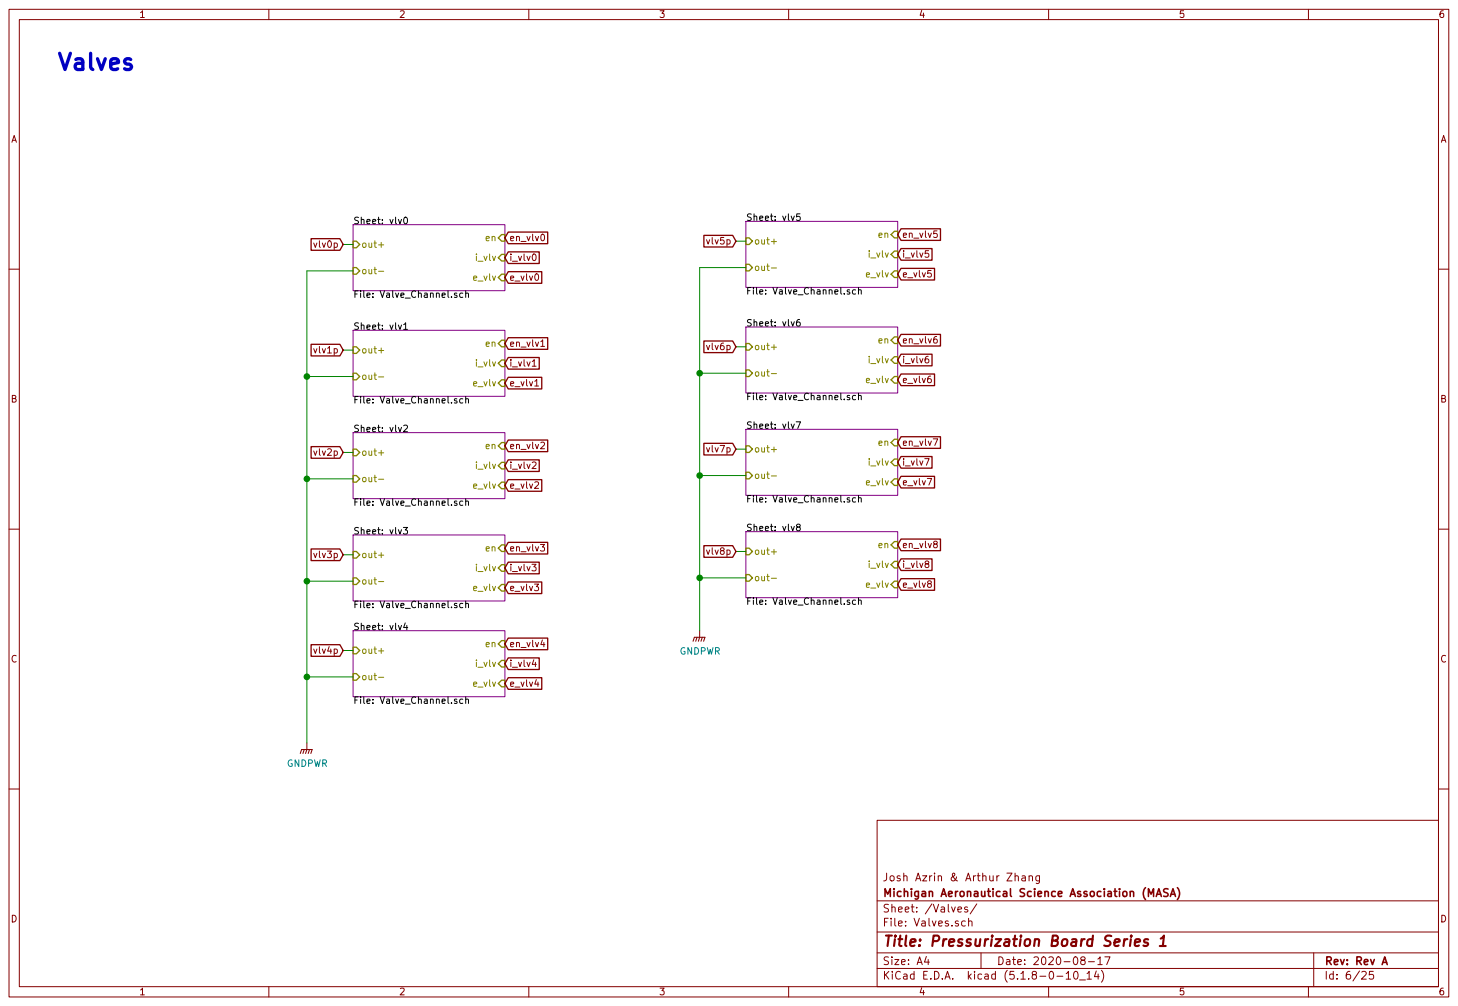
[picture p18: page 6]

Josh Azrin & Arthur Zhang
File: Valves.sch Sheet: /Valves/ Michigan Aeronautical Science Association (MASA)

Id: 6/25 Title: Pressurization Board Series 1

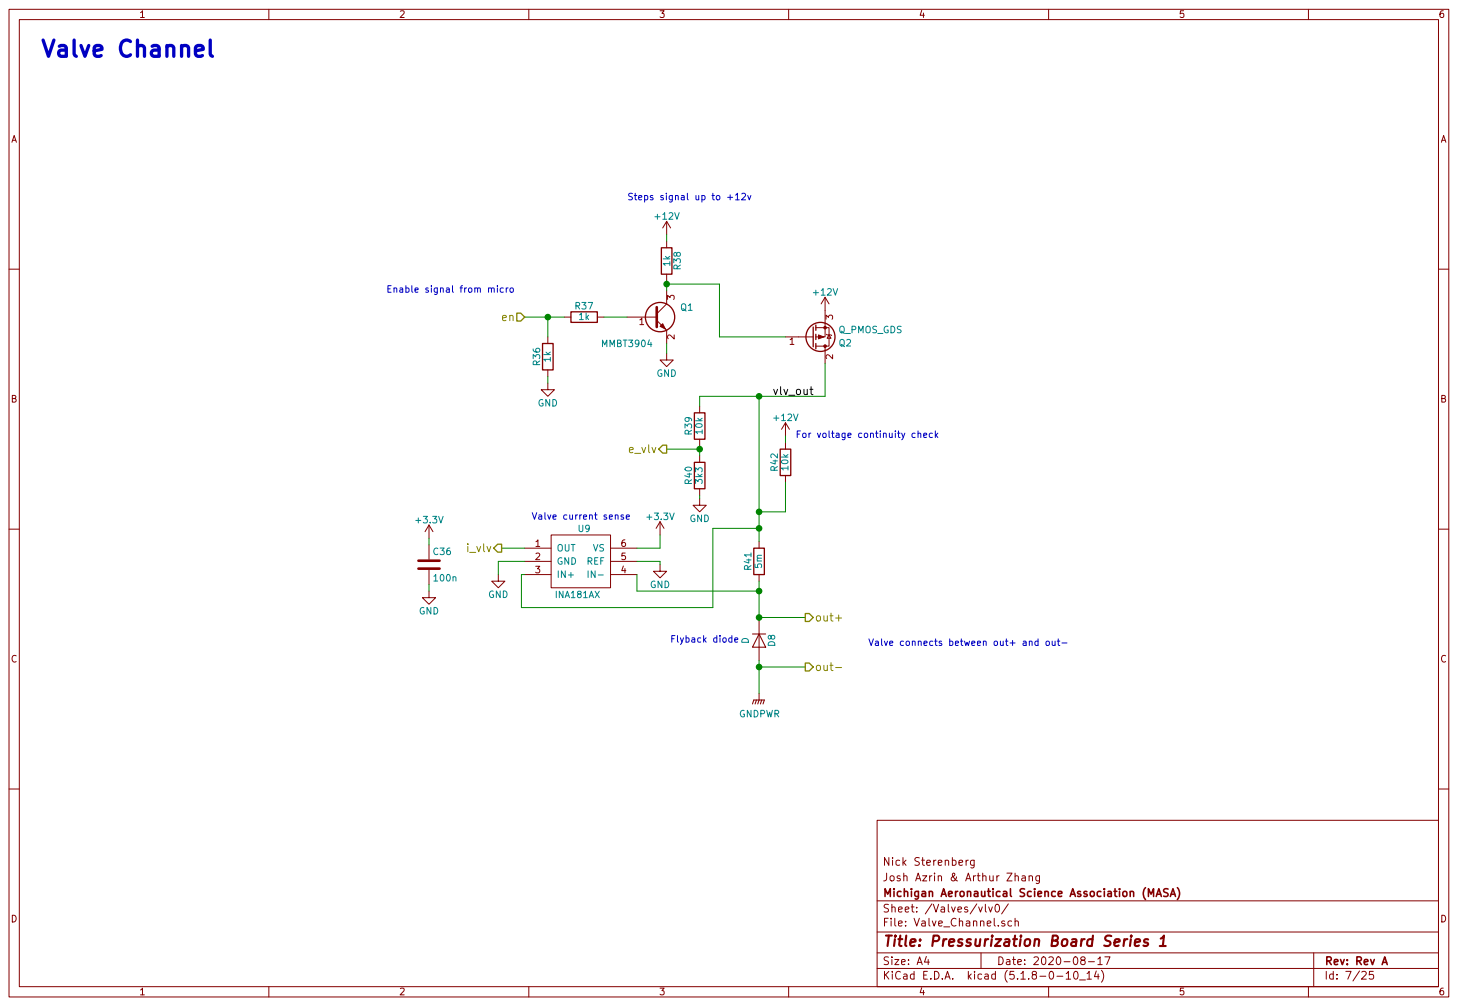
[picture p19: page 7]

Steps signal up to +12v

For voltage continuity check

Nick Sterenberg
Josh Azrin & Arthur Zhang
File: Valve_Channel.sch Sheet: /Valves/vlv0/ Michigan Aeronautical Science Association (MASA)

Id: 7/25 Title: Pressurization Board Series 1

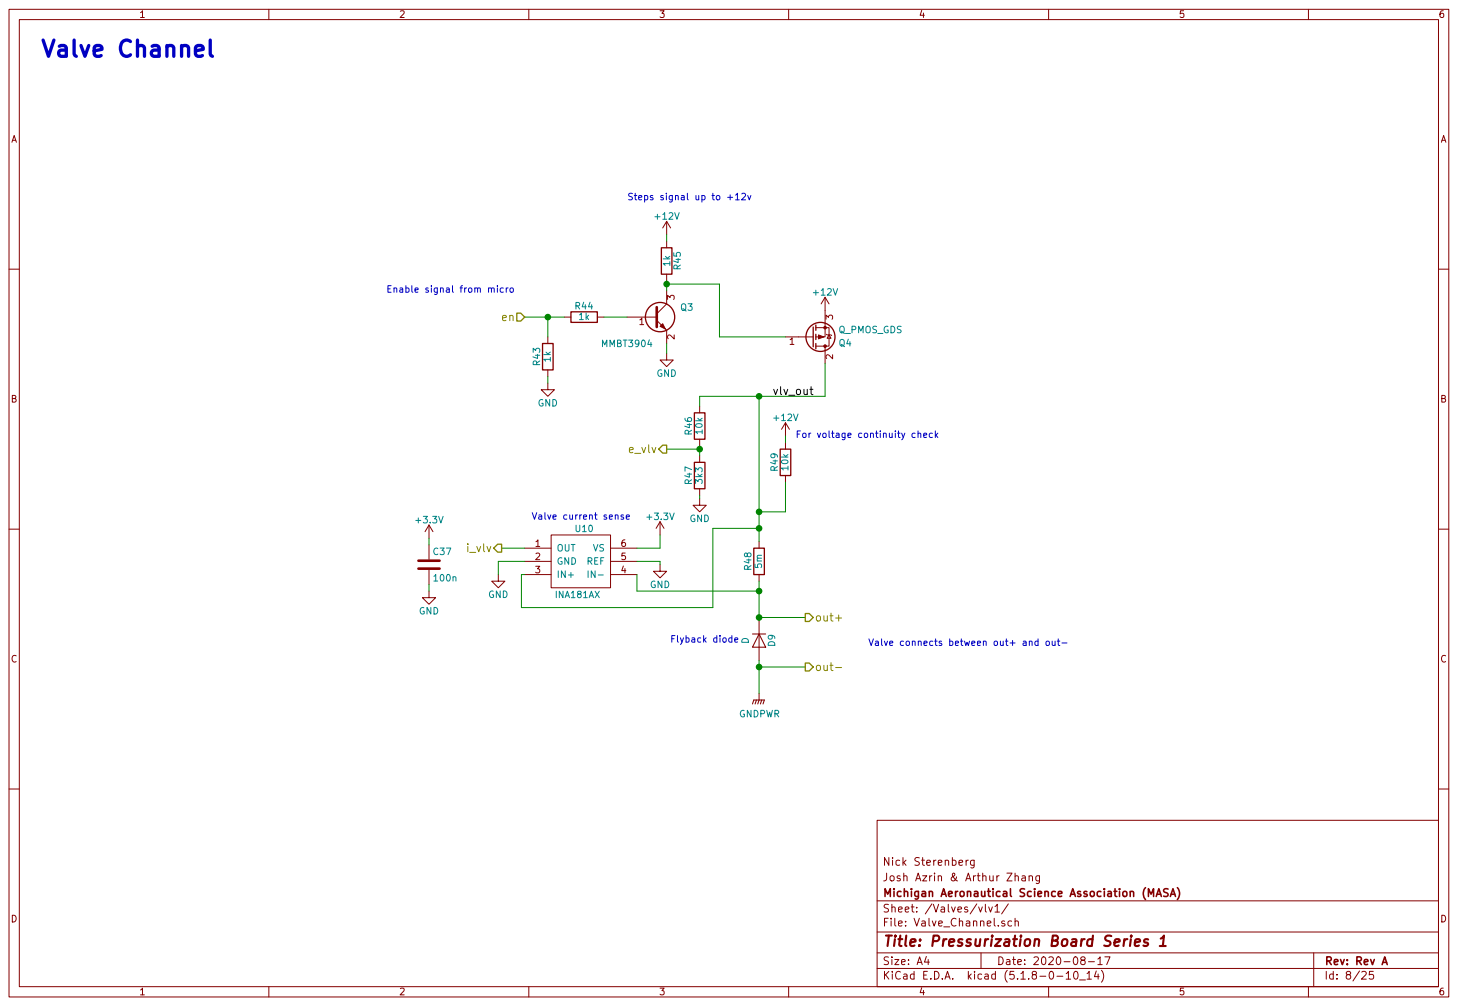
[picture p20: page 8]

Steps signal up to +12v

For voltage continuity check

Nick Sterenberg
Josh Azrin & Arthur Zhang
File: Valve_Channel.sch Sheet: /Valves/vlv1/ Michigan Aeronautical Science Association (MASA)

Id: 8/25 Title: Pressurization Board Series 1

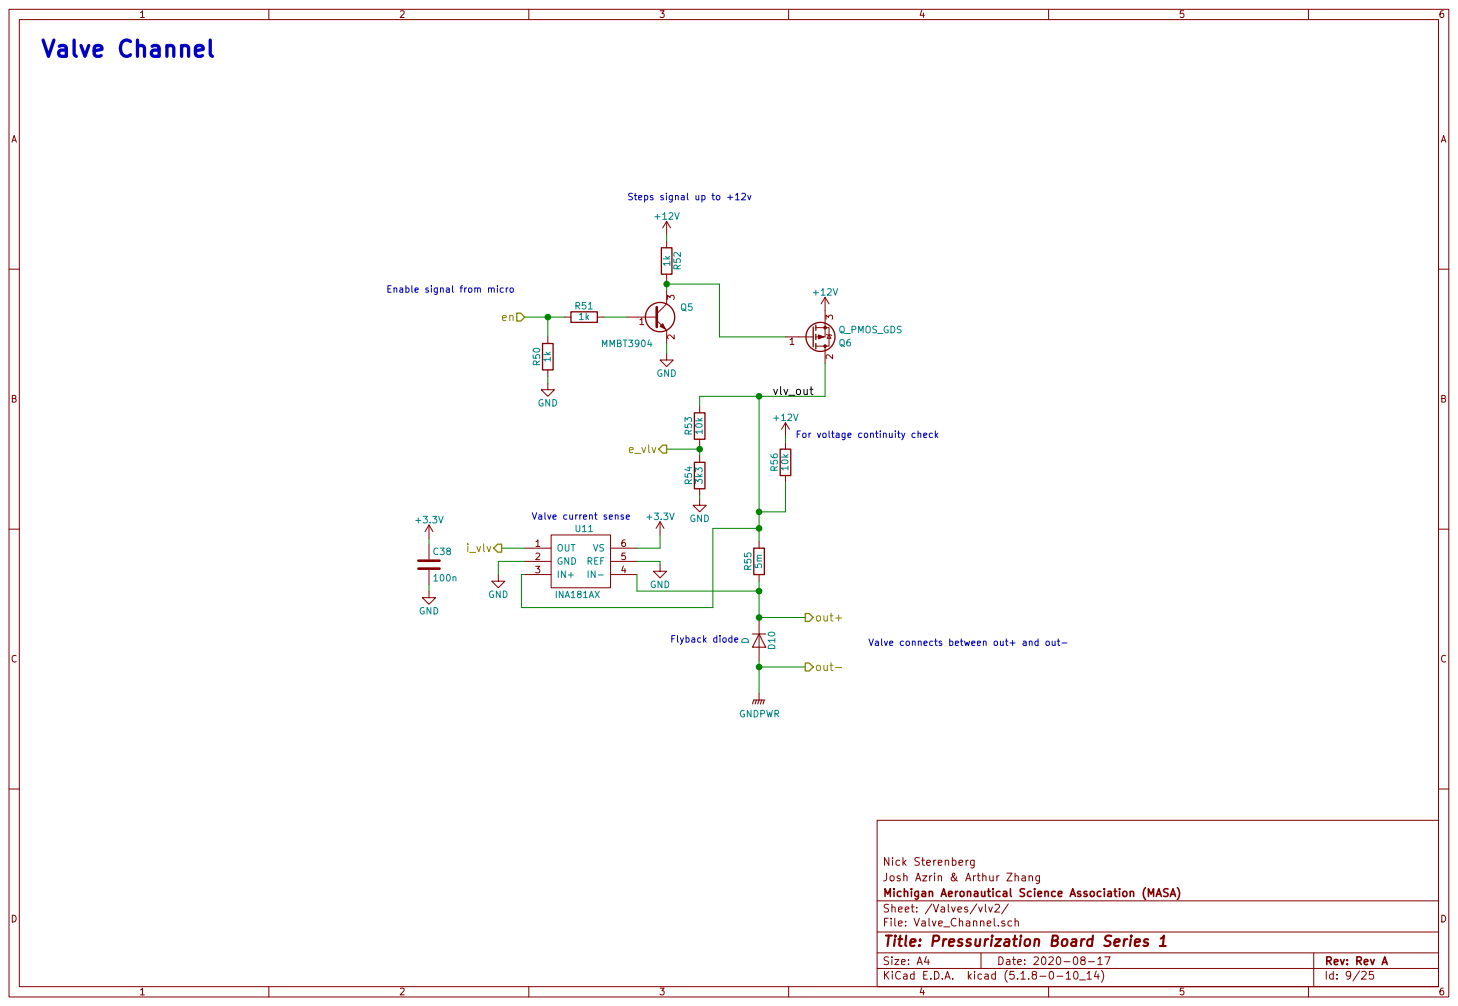
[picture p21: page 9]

Steps signal up to +12v

For voltage continuity check

Nick Sterenberg
Josh Azrin & Arthur Zhang
File: Valve_Channel.sch Sheet: /Valves/vlv2/ Michigan Aeronautical Science Association (MASA)

Id: 9/25 Title: Pressurization Board Series 1

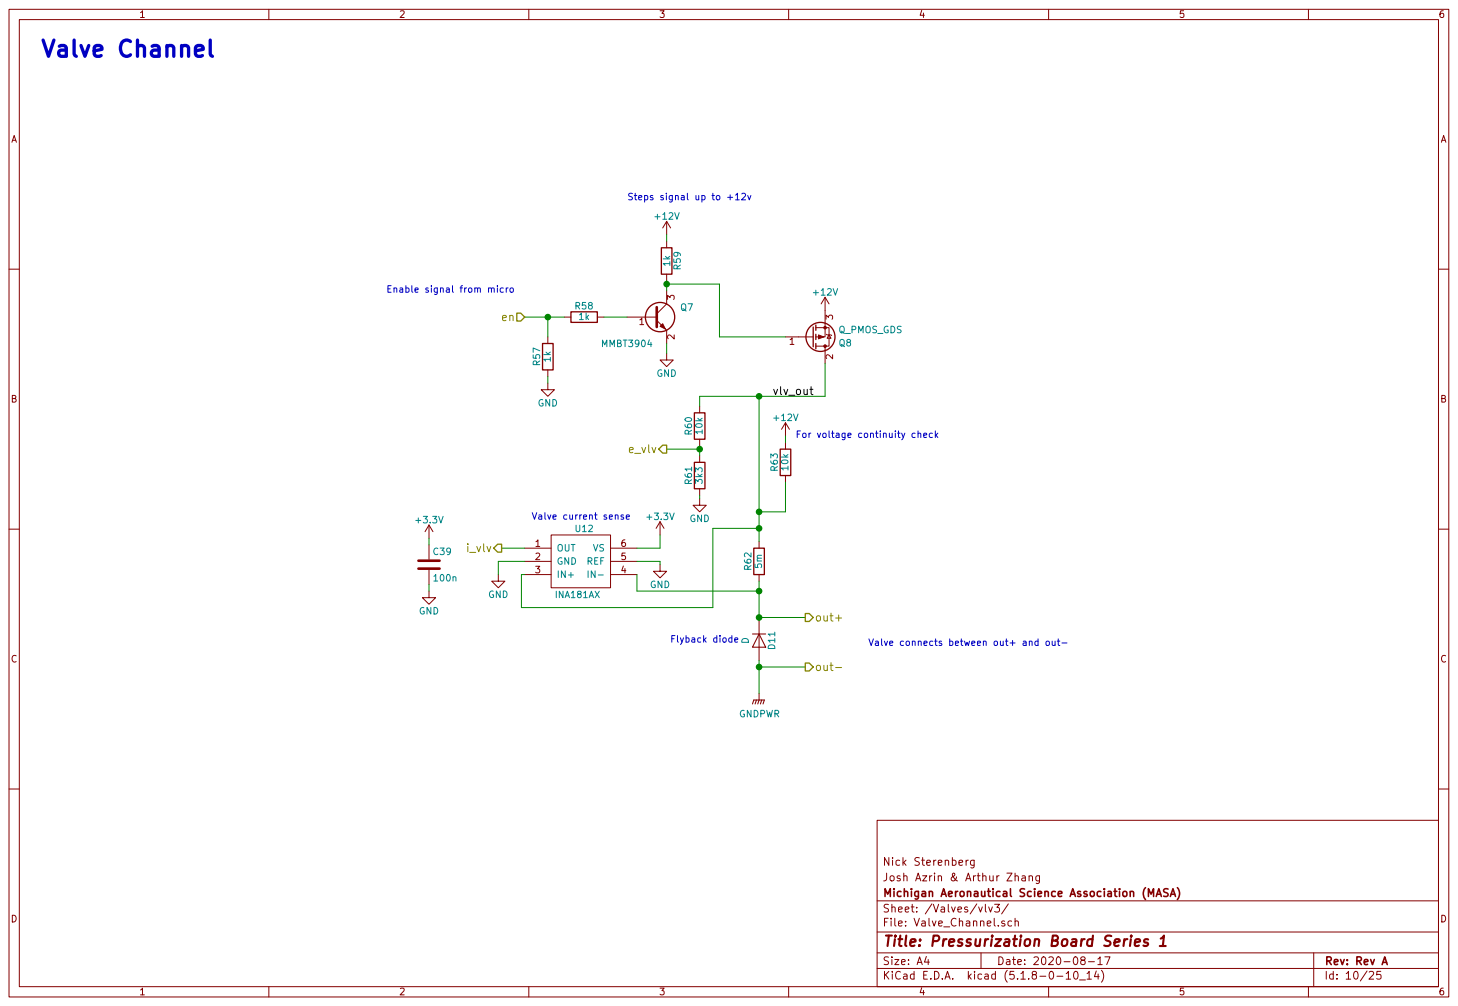
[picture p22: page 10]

Steps signal up to +12v

For voltage continuity check

Nick Sterenberg
Josh Azrin & Arthur Zhang
File: Valve_Channel.sch Sheet: /Valves/vlv3/ Michigan Aeronautical Science Association (MASA)

Id: 10/25 Title: Pressurization Board Series 1

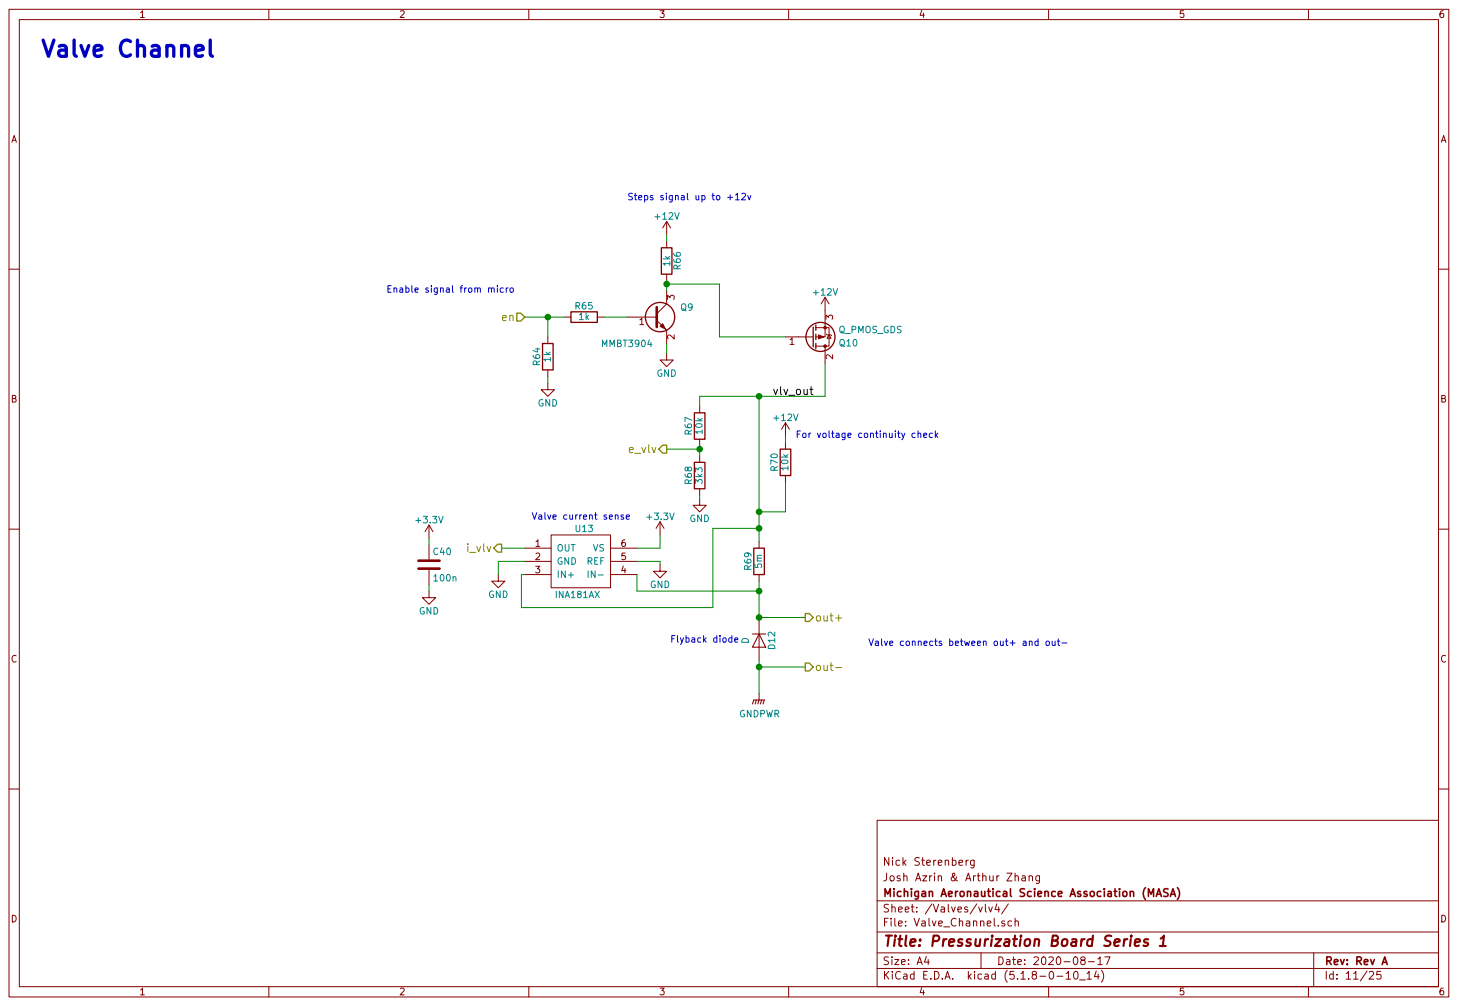
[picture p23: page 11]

Steps signal up to +12v

For voltage continuity check

Nick Sterenberg
Josh Azrin & Arthur Zhang
File: Valve_Channel.sch Sheet: /Valves/vlv4/ Michigan Aeronautical Science Association (MASA)

Id: 11/25 Title: Pressurization Board Series 1

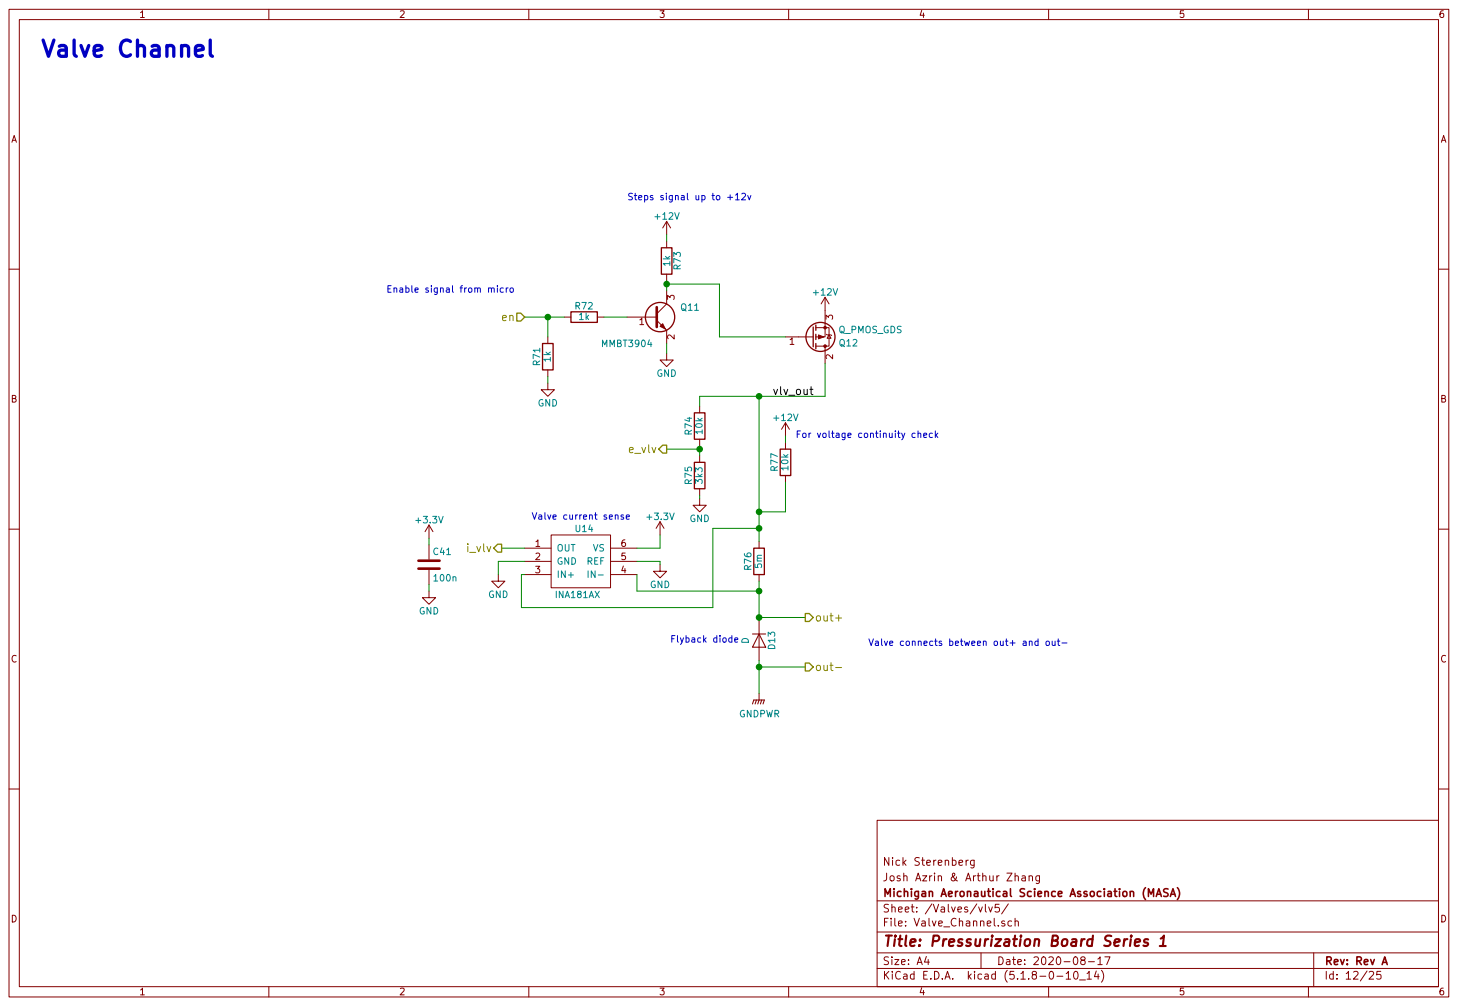
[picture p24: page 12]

Steps signal up to +12v

For voltage continuity check

Nick Sterenberg
Josh Azrin & Arthur Zhang
File: Valve_Channel.sch Sheet: /Valves/vlv5/ Michigan Aeronautical Science Association (MASA)

Id: 12/25 Title: Pressurization Board Series 1

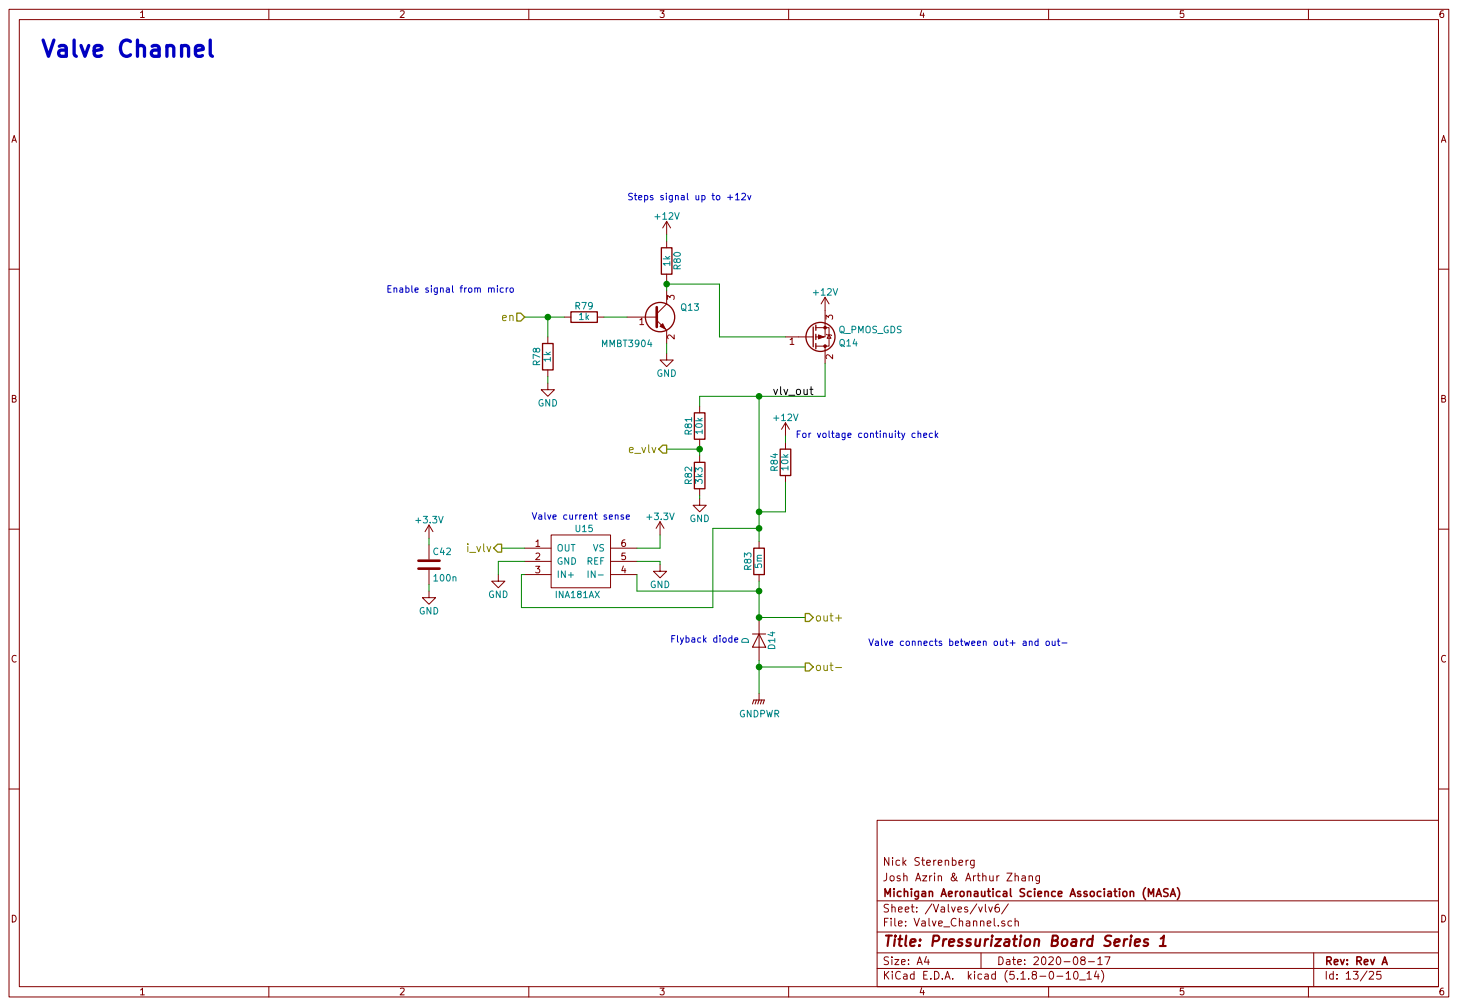
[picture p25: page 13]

Steps signal up to +12v

For voltage continuity check

Nick Sterenberg
Josh Azrin & Arthur Zhang
File: Valve_Channel.sch Sheet: /Valves/vlv6/ Michigan Aeronautical Science Association (MASA)

Id: 13/25 Title: Pressurization Board Series 1


Steps signal up to +12v

For voltage continuity check

Nick Sterenberg
Josh Azrin & Arthur Zhang
File: Valve_Channel.sch Sheet: /Valves/vlv7/ Michigan Aeronautical Science Association (MASA)

Id: 14/25 Title: Pressurization Board Series 1


Steps signal up to +12v

For voltage continuity check
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

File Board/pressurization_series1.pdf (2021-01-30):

Josh Azrin & Arthur Zhang
File: pressurization_series1.sch Sheet: / Michigan Aeronautical Science Association (MASA)

Id: 1/25 Title: Pressurization Board Series 1


Pts can be powered be either 5v or 12v

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

Josh Azrin & Arthur Zhang
File: PressureTransducers.sch Sheet: /Pressure Transducers/ Michigan Aeronautical Science Association (MASA)

Id: 2/25 Title: Pressurization Board Series 1

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


en_vlv6 NRST
mtr1_pwmA GPIO_0
SPI1_MISO
to the oscillator as possible to reduce interferences. J Link

from layout/testing. Total series ressitance,

including trace resistance,
of spi line should = about 50 ohms

Because SPI4 runs in half duplex slave mode, SPI4_MOSI is not needed.

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

Capacitors should be placed as close to the microcontroller as possible to reduce interferences

100n capacitor should
be placed as close

Josh Azrin & Arthur Zhang
File: Microcontroller.sch Sheet: /Microcontroller/ Michigan Aeronautical Science Association (MASA)

Id: 4/25 Title: Pressurization Board Series 1


+3.3V line for many ICs

Precise 3.3v line used for adcs 12 clean, less noisy 12v line

Gndpwr is noisy ground that connects to high current devices (vlvs, mtrs)

Nick Sterenberg
Josh Azrin & Arthur Zhang
File: Power.sch Sheet: /Power/ Michigan Aeronautical Science Association (MASA)

Id: 5/25 Title: Pressurization Board Series 1


Josh Azrin & Arthur Zhang
File: Valves.sch Sheet: /Valves/ Michigan Aeronautical Science Association (MASA)

Id: 6/25 Title: Pressurization Board Series 1


Steps signal up to +12v

For voltage continuity check

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

Id: 7/25 Title: Pressurization Board Series 1


Steps signal up to +12v

For voltage continuity check

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

Id: 8/25 Title: Pressurization Board Series 1


Steps signal up to +12v

For voltage continuity check

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

Id: 9/25 Title: Pressurization Board Series 1


Steps signal up to +12v

For voltage continuity check

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

Id: 10/25 Title: Pressurization Board Series 1


Steps signal up to +12v

For voltage continuity check

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

Id: 11/25 Title: Pressurization Board Series 1


Steps signal up to +12v

For voltage continuity check

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

Id: 12/25 Title: Pressurization Board Series 1


Steps signal up to +12v

For voltage continuity check

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

Id: 13/25 Title: Pressurization Board Series 1


Steps signal up to +12v

For voltage continuity check

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

Id: 14/25 Title: Pressurization Board Series 1


Steps signal up to +12v

For voltage continuity check
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







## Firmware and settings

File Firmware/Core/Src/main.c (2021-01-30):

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
/* Includes ------------------------------------------------------------------*/
#include "main.h"

SPI_HandleTypeDef hspi1;
SPI_HandleTypeDef hspi2;
SPI_HandleTypeDef hspi4;

TIM_HandleTypeDef htim1;
TIM_HandleTypeDef htim2;
TIM_HandleTypeDef htim3;
TIM_HandleTypeDef htim6;
TIM_HandleTypeDef htim7;
TIM_HandleTypeDef htim8;
TIM_HandleTypeDef htim9;
TIM_HandleTypeDef htim10;
TIM_HandleTypeDef htim11;

UART_HandleTypeDef huart1;
UART_HandleTypeDef huart2;

void SystemClock_Config(void);
static void MX_GPIO_Init(void);
static void MX_SPI1_Init(void);
static void MX_TIM1_Init(void);
static void MX_SPI2_Init(void);
static void MX_SPI4_Init(void);
static void MX_TIM8_Init(void);
static void MX_USART1_UART_Init(void);
static void MX_USART2_UART_Init(void);
static void MX_TIM2_Init(void);
static void MX_TIM6_Init(void);
static void MX_TIM7_Init(void);
static void MX_TIM10_Init(void);
static void MX_TIM11_Init(void);
static void MX_TIM3_Init(void);
static void MX_TIM9_Init(void);
/* USER CODE BEGIN 0 */
volatile int check_board_alive  = 1;
uint64_t prev_time              = 0;
uint16_t adc_counts[3][16];  // array for receiving adc conversions
GPIO_MAX11131_Pinfo adc_pins[3];
uint8_t telem_buffer[2048];
uint8_t last_byte_uart;
volatile uint16_t telem_buffer_sz = 0;
W25N01GV_Flash flash;

volatile uint8_t send_telem          = 0;
volatile uint8_t do_calculations     = 0;
volatile uint8_t save_flash          = 0;
volatile uint8_t read_peripherals    = 0;

// Control Loop Variables

//Sensor Values
float *sensorTop = &pressure[0]; // declared this way explicitly for clarity
float *sensorBot = &pressure[1];
float *sensorPres = &pressure[2];

//Pressure Values
float PresTop = 0;
float PresBot = 0;
float PresPres = 0;

double topSlope = 1.95503421;
double topOffset = 0;

double botSlope = 0.36656891;
double botOffset = -37.39;

double presSlope = 1.95503421;
double presOffset = -207.23-3.91;

//-----------------------------------------------------------------------------------------------

//Solenoid Position
uint16_t pOpen = 0;
uint16_t dOpen = 0;

uint8_t testState = 0;
uint8_t testDone = 0;

//----------------------------------------------------------------------------------------------
//Stepper Initializations
uint16_t step_step = 9;
uint16_t ms1 = 10;
uint16_t ms2 = 11;
float degChange;
float delta;
double degPerStep = 0.35;
uint16_t delay_between_steps = 500; //microseconds. 1000 microseconds in a ms.

//----------------------------------------------------------------------------------------------
//Propellant Tank Target Pressure
float Setpoint = 40.;
uint32_t init_time = 0.;

//Test Variables
float ullage = 1.313; //lbs
uint32_t endTime = 30.*1000.+10000.; //milliseconds

//---------------------------------------------------------------------------------------------
//PID variables
uint32_t lastTime = 10000;
double errSum = 0;
double last_error;
double kp_term, ki_term, kd_term;
double timeChange, error, pi_change;
uint32_t now = 0;

// stepper tracking
float targetPos = 0;
float curPos = 0;

uint32_t ctrl_dt = 100;  // control period in milliseconds

// Stepper motor linear ramp variables
uint8_t step_stage = 0; // polarity of stepper motor coils

Stepper_Ramping stepper;

void init_control_variables() {
    curDir = 1; // TODO: change back to 0 initialize to 0 to force startup intialization
    STATE     = Idle;
    last_error = Setpoint;
    kp = 5;
    ki = 2;
    kd = 3;
    initAdcs(&hspi1, adc_pins);   // initialize adcs
    init_flash(&flash, &hspi2, FLASH_CS_GPIO_Port ,FLASH_CS_Pin);
    HAL_UART_Receive_IT(&huart2, &last_byte_uart, 1); // init comms
    /*for (uint8_t i = 0; i < 9; ++i) {
    	setValve(i, 0); // set all valves low
    }*/

    // init stepper ramping variables
    stepper.v_0 = 1000; // based off of timer configuration of 1ms per step
    stepper.v = 2000; // target num of steps per second
    stepper.a = 1000; // set initial acceleration to 5 steps/sec/sec
    stepper.F = 1000; // frequency set to 1 kHz update time
    stepper.R = stepper.a / (stepper.F * stepper.F); // constant from a/F^2
    stepper.ps = stepper.F / stepper.v; // slew speed constant
    stepper.p1 = stepper.F / 1001; // denom precomputed sqrt(v0+2a)
    stepper.S = (stepper.v*stepper.v-stepper.v_0*stepper.v_0) / (2*stepper.a);
    stepper.p = stepper.p1; // initially p is p1
}

void readPeripherals() {
	readAdcs(&hspi1, adc_pins, adc_counts);
    updatePeripherals(adc_counts);
    read_peripherals = 0;
}

void HAL_UART_RxCpltCallback(UART_HandleTypeDef *huart) {
    if (huart == &huart2) {
        HAL_UART_Receive_IT(&huart2, &last_byte_uart, 1);
        telem_buffer[telem_buffer_sz++] = last_byte_uart;
    }
}

void HAL_TIM_PeriodElapsedCallback(TIM_HandleTypeDef* htim)
{
    if (htim == &htim6) {               // Period: 1 ms    (1kHz)
        // step the motor
        //if (targetPos != curPos) {
            if(step_stage == 4) {
                step_stage = 0;
            } // reset step stage if reached
            turn_stepper_motor(&htim2, 0, curDir, step_stage); // timer 3 is used for motor 0
            ++step_stage;
            // uncomment code below for dynamic stepping
            //computeStepperRamp(&stepper);
            //changeStepperPeriod(&htim6, &stepper);
            curPos = curPos + degPerStep*curDir;
        //}
    } else if (htim == &htim7) {        // Period: 5 ms     (200Hz)
        if (STATE == Running) {
            save_flash = 1;
            read_peripherals = 1;
        }
    } else if (htim == &htim10) {       // Period: 10 ms    (100Hz)
        if (STATE == Running) {
            do_calculations = 1;
        }
    } else if (htim == &htim11) {       // Period: 100ms    (10 Hz)
        // always send telem
        send_telem = 1;
    }
}

uint64_t getCurrentTime() {
    uint64_t current_time = HAL_GetTick() - prev_time;
    prev_time = current_time;
    return current_time; // returns time elapsed in milliseconds
}

void sendTelem() {
    if (send_telem == 1) {
        // TODO: add in feature only send some telem if slowing down loop
    	send_telem_packet(&huart2, NULL, telem_packet, -1); // send all telem
        send_telem = 0;
    }
}

void doCalculations() {
    if (do_calculations == 1) {
        if (testDone==0) {
            //Standard BangBang Control
            HAL_GPIO_WritePin(SolenoidPortD, SolenoidPinD, GPIO_PIN_SET);
            dOpen = 1;

            // Execute control solenoid safety loop
            if (PresBot < Setpoint*.95 && pOpen == 0){
                HAL_GPIO_WritePin(SolenoidPortP, SolenoidPinP, GPIO_PIN_SET);
                pOpen = 1;
            } else if (PresBot > Setpoint*1.1 && pOpen == 1){
                HAL_GPIO_WritePin(SolenoidPortP, SolenoidPinP, GPIO_PIN_RESET);
                pOpen = 0;
            }

            // Stepping Actuation
            if (targetPos < curPos && curDir != -1) {  // only write dir pin if it hasn't been written before
                curDir = -1;
            } else if (targetPos > curPos && curDir != 1) {
                curDir = 1;
            }
            now = HAL_GetTick();    // returns time in ms since startup

            if ( now - lastTime > ctrl_dt ) {
              //Reads in sensor values and converts to Psi
              // pressure values were last sampled

              PresTop = topSlope * *sensorTop + topOffset;
              PresBot = botSlope * *sensorBot + botOffset;
              PresPres = presSlope * *sensorPres + presOffset;

              //-------------------------------------------------------------------------------------------------
              //Control Loop
              // Calculate PI loop
              timeChange = (now - lastTime)/1000.0;
              error = Setpoint - PresBot;
              errSum += error * timeChange;
              kp_term =  kp * error;
              ki_term = ki * errSum;
              kd_term = kd * (error - last_error) / timeChange;
              pi_change = kp_term + ki_term + kd_term;
              if (pi_change > 0) {
                delta = ((7 * 360 - 60 - curPos) <  pi_change) ? (7 * 360 - 60 - curPos) : pi_change;; // TODO: use a macro/precompute
              }
              else {
                delta = -curPos > pi_change;
              }
              targetPos = curPos + delta;
              last_error = error;
              lastTime = now;
            }
        }
        do_calculations = 0;
    }
}

void saveFlash() {
    if (save_flash == 1) {
        // automatically packs telem data to flash
        save_telem_to_flash(&flash);
        //send_telem_from_flash(&flash, &huart2); //used for testing sending from flash
        save_flash = 0;
    }
}


/* USER CODE END 0 */

/**
  * @brief  The application entry point.
  * @retval int
  */
int main(void)
{
  /* MCU Configuration--------------------------------------------------------*/

  /* Reset of all peripherals, Initializes the Flash interface and the Systick. */
  HAL_Init();

  /* Configure the system clock */
  SystemClock_Config();

  /* Initialize all configured peripherals */
  MX_GPIO_Init();
  MX_SPI1_Init();
  MX_TIM1_Init();
  MX_SPI2_Init();
  MX_SPI4_Init();
  MX_TIM8_Init();
  MX_USART1_UART_Init();
  MX_USART2_UART_Init();
  MX_TIM2_Init();
  MX_TIM6_Init();
  MX_TIM7_Init();
  MX_TIM10_Init();
  MX_TIM11_Init();
  MX_TIM3_Init();
  MX_TIM9_Init();
  /* USER CODE BEGIN 2 */
  HAL_TIM_Base_Start_IT(&htim9);	// initializes timer for checking LED alive status
  HAL_TIM_Base_Start_IT(&htim6);	// starts stepper motor
  HAL_TIM_Base_Start_IT(&htim7);	// starts save to flash and reads peripherals
  HAL_TIM_Base_Start_IT(&htim10);	// starts doing calculations
  HAL_TIM_Base_Start_IT(&htim11);	// starts sending telem
  init_control_variables();			// initializes constants

  /* USER CODE END 2 */

  /* Infinite loop */
  /* USER CODE BEGIN WHILE */
  while (1)
  {
    /* USER CODE END WHILE */

    /* USER CODE BEGIN 3 */
    if (telem_buffer_sz >= PONG_MAX_PACKET_SIZE) {
        receive_data(&huart2, telem_buffer, telem_buffer_sz);
        telem_buffer_sz = 0;
    }
	if (STATE==Idle) {
		readPeripherals();
		sendTelem();
    } else if (STATE==Armed) {
        readPeripherals();
        sendTelem();
    } else if (STATE==Running) {
        readPeripherals();
        doCalculations();
        sendTelem();
        saveFlash();
    } else {
        // TODO: close solenoid p and d
        // TODO: finish_flash_write(flash); should only be called when we send telem back to ground
        readPeripherals();
        sendTelem();
    } // default condition to stop
  }
  /* USER CODE END 3 */
}

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


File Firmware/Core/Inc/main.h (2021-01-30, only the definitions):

#define en_vlv8_Pin GPIO_PIN_2
#define en_vlv8_GPIO_Port GPIOE
#define en_vlv7_Pin GPIO_PIN_3
#define en_vlv7_GPIO_Port GPIOE
#define en_vlv6_Pin GPIO_PIN_4
#define en_vlv6_GPIO_Port GPIOE
#define en_vlv5_Pin GPIO_PIN_5
#define en_vlv5_GPIO_Port GPIOE
#define en_vlv4_Pin GPIO_PIN_6
#define en_vlv4_GPIO_Port GPIOE
#define en_vlv3_Pin GPIO_PIN_13
#define en_vlv3_GPIO_Port GPIOC
#define en_vlv2_Pin GPIO_PIN_14
#define en_vlv2_GPIO_Port GPIOC
#define en_vlv1_Pin GPIO_PIN_15
#define en_vlv1_GPIO_Port GPIOC
#define LED0_Pin GPIO_PIN_0
#define LED0_GPIO_Port GPIOC
#define LED1_Pin GPIO_PIN_1
#define LED1_GPIO_Port GPIOC
#define LED2_Pin GPIO_PIN_2
#define LED2_GPIO_Port GPIOC
#define LED3_Pin GPIO_PIN_3
#define LED3_GPIO_Port GPIOC
#define e_hall1A_Pin GPIO_PIN_0
#define e_hall1A_GPIO_Port GPIOA
#define e_hall1B_Pin GPIO_PIN_1
#define e_hall1B_GPIO_Port GPIOA
#define e_hall1C_Pin GPIO_PIN_2
#define e_hall1C_GPIO_Port GPIOA
#define adc0_cs_Pin GPIO_PIN_3
#define adc0_cs_GPIO_Port GPIOA
#define adc0_eoc_Pin GPIO_PIN_4
#define adc0_eoc_GPIO_Port GPIOA
#define adc0_cnvst_Pin GPIO_PIN_4
#define adc0_cnvst_GPIO_Port GPIOC
#define adc1_eoc_Pin GPIO_PIN_5
#define adc1_eoc_GPIO_Port GPIOC
#define adc1_cs_Pin GPIO_PIN_0
#define adc1_cs_GPIO_Port GPIOB
#define adc1_cnvst_Pin GPIO_PIN_1
#define adc1_cnvst_GPIO_Port GPIOB
#define adc2_cs_Pin GPIO_PIN_2
#define adc2_cs_GPIO_Port GPIOB
#define adc2_eoc_Pin GPIO_PIN_7
#define adc2_eoc_GPIO_Port GPIOE
#define adc2_cnvst_Pin GPIO_PIN_8
#define adc2_cnvst_GPIO_Port GPIOE
#define tc0_cs_Pin GPIO_PIN_9
#define tc0_cs_GPIO_Port GPIOE
#define tc1_cs_Pin GPIO_PIN_10
#define tc1_cs_GPIO_Port GPIOE
#define tc2_cs_Pin GPIO_PIN_11
#define tc2_cs_GPIO_Port GPIOE
#define tc3_cs_Pin GPIO_PIN_15
#define tc3_cs_GPIO_Port GPIOE
#define tc4_cs_Pin GPIO_PIN_10
#define tc4_cs_GPIO_Port GPIOB
#define SD_CS_Pin GPIO_PIN_12
#define SD_CS_GPIO_Port GPIOB
#define FLASH_CS_Pin GPIO_PIN_8
#define FLASH_CS_GPIO_Port GPIOD
#define mtr2_in0_Pin GPIO_PIN_9
#define mtr2_in0_GPIO_Port GPIOD
#define mtr2_in1_Pin GPIO_PIN_10
#define mtr2_in1_GPIO_Port GPIOD
#define mtr2_in2_Pin GPIO_PIN_11
#define mtr2_in2_GPIO_Port GPIOD
#define e_hall0A_Pin GPIO_PIN_12
#define e_hall0A_GPIO_Port GPIOD
#define e_hall0B_Pin GPIO_PIN_13
#define e_hall0B_GPIO_Port GPIOD
#define e_hall0C_Pin GPIO_PIN_14
#define e_hall0C_GPIO_Port GPIOD
#define mtr2_pwm0_Pin GPIO_PIN_6
#define mtr2_pwm0_GPIO_Port GPIOC
#define mtr2_pwm1_Pin GPIO_PIN_7
#define mtr2_pwm1_GPIO_Port GPIOC
#define mtr2_pwm2_Pin GPIO_PIN_8
#define mtr2_pwm2_GPIO_Port GPIOC
#define mtr0_inB0_Pin GPIO_PIN_9
#define mtr0_inB0_GPIO_Port GPIOC
#define mtr3_pwm0_Pin GPIO_PIN_8
#define mtr3_pwm0_GPIO_Port GPIOA
#define mtr3_pwm1_Pin GPIO_PIN_9
#define mtr3_pwm1_GPIO_Port GPIOA
#define mtr3_pwm2_Pin GPIO_PIN_10
#define mtr3_pwm2_GPIO_Port GPIOA
#define mtr0_inB1_Pin GPIO_PIN_11
#define mtr0_inB1_GPIO_Port GPIOA
#define GPIO_3_Pin GPIO_PIN_12
#define GPIO_3_GPIO_Port GPIOA
#define mtr0_inA0_Pin GPIO_PIN_10
#define mtr0_inA0_GPIO_Port GPIOC
#define mtr0_inA1_Pin GPIO_PIN_11
#define mtr0_inA1_GPIO_Port GPIOC
#define mtr3_in0_Pin GPIO_PIN_12
#define mtr3_in0_GPIO_Port GPIOC
#define mtr3_in1_Pin GPIO_PIN_0
#define mtr3_in1_GPIO_Port GPIOD
#define mtr3_in2_Pin GPIO_PIN_1
#define mtr3_in2_GPIO_Port GPIOD
#define mtr1_inA0_Pin GPIO_PIN_2
#define mtr1_inA0_GPIO_Port GPIOD
#define mtr1_inA1_Pin GPIO_PIN_3
#define mtr1_inA1_GPIO_Port GPIOD
#define mtr1_inB0_Pin GPIO_PIN_4
#define mtr1_inB0_GPIO_Port GPIOD
#define mtr1_inB1_Pin GPIO_PIN_7
#define mtr1_inB1_GPIO_Port GPIOD
#define mtr1_pwmA_Pin GPIO_PIN_4
#define mtr1_pwmA_GPIO_Port GPIOB
#define mtr1_pwmB_Pin GPIO_PIN_5
#define mtr1_pwmB_GPIO_Port GPIOB
#define mtr0_pwmA_Pin GPIO_PIN_8
#define mtr0_pwmA_GPIO_Port GPIOB
#define mtr0_pwmB_Pin GPIO_PIN_9
#define mtr0_pwmB_GPIO_Port GPIOB
#define GPIO_1_Pin GPIO_PIN_0
#define GPIO_1_GPIO_Port GPIOE
#define en_vlv0_Pin GPIO_PIN_1
#define en_vlv0_GPIO_Port GPIOE
#define SolenoidPinD    en_vlv0_Pin
#define SolenoidPortD   en_vlv0_GPIO_Port
#define SolenoidPinP    en_vlv1_Pin
#define SolenoidPortP   en_vlv1_GPIO_Port
#define StepDirPin      en_vlv2_Pin
#define StepDirPort     en_vlv2_GPIO_Port
#define StepStepPin     en_vlv3_Pin
#define StepStepPort    en_vlv3_GPIO_Port

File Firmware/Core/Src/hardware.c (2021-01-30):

#include "hardware.h"

void initAdcs(SPI_HandleTypeDef* hspix, GPIO_MAX11131_Pinfo *adc_pins) {
    adc_pins[0].MAX11131_CS_PORT       = adc0_cs_GPIO_Port;
    adc_pins[0].MAX11131_EOC_PORT      = adc0_eoc_GPIO_Port;
    adc_pins[0].MAX11131_CNVST_PORT    = adc0_cnvst_GPIO_Port;
    adc_pins[0].MAX11131_CS_ADDR       = adc0_cs_Pin;
    adc_pins[0].MAX11131_EOC_ADDR      = adc0_eoc_Pin;
    adc_pins[0].MAX11131_CNVST_ADDR    = adc0_cnvst_Pin;
    adc_pins[1].MAX11131_CS_PORT       = adc1_cs_GPIO_Port;
    adc_pins[1].MAX11131_EOC_PORT      = adc1_eoc_GPIO_Port;
    adc_pins[1].MAX11131_CNVST_PORT    = adc1_cnvst_GPIO_Port;
    adc_pins[1].MAX11131_CS_ADDR       = adc1_cs_Pin;
    adc_pins[1].MAX11131_EOC_ADDR      = adc1_eoc_Pin;
    adc_pins[1].MAX11131_CNVST_ADDR    = adc1_cnvst_Pin;
    adc_pins[2].MAX11131_CS_PORT       = adc2_cs_GPIO_Port;
    adc_pins[2].MAX11131_EOC_PORT      = adc2_eoc_GPIO_Port;
    adc_pins[2].MAX11131_CNVST_PORT    = adc2_cnvst_GPIO_Port;
    adc_pins[2].MAX11131_CS_ADDR       = adc2_cs_Pin;
    adc_pins[2].MAX11131_EOC_ADDR      = adc2_eoc_Pin;
    adc_pins[2].MAX11131_CNVST_ADDR    = adc2_cnvst_Pin;
    init_adc(hspix, &adc_pins[0]);
    init_adc(hspix, &adc_pins[1]);
    init_adc(hspix, &adc_pins[2]);
}

void computeStepperRamp(Stepper_Ramping* stepper) {
    double p = (double) stepper->p;
    double m = 0;
    if ( p < stepper->ps) { // decceleration phase
        p = stepper->ps;
        m = stepper->R;
    } else if (p > stepper->p1) { // acceleration phase
        p = stepper->p1;
        m = -stepper->R;
    }

    stepper->p = p*(1+m*p*p); // compute new delay period
}

void changeStepperPeriod(TIM_HandleTypeDef *htimx, Stepper_Ramping* stepper) {
    uint16_t new_period = (uint16_t)(stepper->p*100000);// convert period from s to 10*us

    // Expected range of new_period <100 (period of 100 gives stepper rate of 1 ms)
    HAL_TIM_Base_Stop_IT(htimx);
    // htimx->Instance =  no need to change instance
    htimx->Init.Prescaler = 15999;
    htimx->Init.CounterMode = TIM_COUNTERMODE_UP;
    htimx->Init.Period = new_period;
    htimx->Init.ClockDivision = TIM_CLOCKDIVISION_DIV1;
    htimx->Init.AutoReloadPreload = TIM_AUTORELOAD_PRELOAD_DISABLE;
    HAL_TIM_Base_Init(htimx);

    HAL_TIM_Base_Start_IT(htimx);
}

void turn_stepper_motor(TIM_HandleTypeDef *htimx, uint8_t motor_num, int8_t direction, uint8_t step_stage) {
    // A+
    // B+
    // A-
    // B-
    // For VNH7070AS chip, INA = clockwise, INB = counterclockwise
    // reset all gpio logic before changing step
    // Note: this only works for motor 0 currently 1 is CW, -1 is CCW
	GPIO_TypeDef * mtrx_portA0 = motor_num ? mtr1_inA0_GPIO_Port : mtr0_inA0_GPIO_Port;
	GPIO_TypeDef * mtrx_portA1 = motor_num ? mtr1_inA1_GPIO_Port : mtr0_inA1_GPIO_Port;
	GPIO_TypeDef * mtrx_portB0 = motor_num ? mtr1_inB0_GPIO_Port : mtr0_inB0_GPIO_Port;
	GPIO_TypeDef * mtrx_portB1 = motor_num ? mtr1_inB1_GPIO_Port : mtr0_inB1_GPIO_Port;
	uint16_t mtrx_pinA0 = motor_num ? mtr1_inA0_Pin : mtr0_inA0_Pin;
	uint16_t mtrx_pinA1 = motor_num ? mtr1_inA1_Pin : mtr0_inA1_Pin;
	uint16_t mtrx_pinB0 = motor_num ? mtr1_inB0_Pin : mtr0_inB0_Pin;
	uint16_t mtrx_pinB1 = motor_num ? mtr1_inB1_Pin : mtr0_inB1_Pin;
	uint32_t pwm_channela = TIM_CHANNEL_1;
	uint32_t pwm_channelb = TIM_CHANNEL_2;
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

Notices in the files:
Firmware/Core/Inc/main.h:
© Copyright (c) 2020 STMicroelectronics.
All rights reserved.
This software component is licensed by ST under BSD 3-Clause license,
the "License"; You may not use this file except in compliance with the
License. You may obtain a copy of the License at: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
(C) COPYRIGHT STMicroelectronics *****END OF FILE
